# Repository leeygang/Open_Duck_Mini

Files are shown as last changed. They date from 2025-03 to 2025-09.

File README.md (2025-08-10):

# Open Duck Mini v2

<table>
  <tr>
    <td> </td>
    <td> </td>
    <td> </td>
   </tr> 
</table>

We are making a miniature version of the BDX Droid by Disney. It is about 42 centimeters tall with its legs extended.
The full BOM cost should be under $400 !

This repo is kind of a hub where we centralize all resources related to this project. This is a working repo, so there are a lot of undocumented scripts :) We'll try to clean things up at some point.

# State of sim2real

https://github.com/user-attachments/assets/58721d0f-2f95-4088-8900-a5d02f41bba7

https://github.com/user-attachments/assets/4129974a-9d97-4651-9474-c078043bb182

https://github.com/user-attachments/assets/a0afcd38-15d8-40c6-8171-a619107406b8

# Updates

> Update 02/04/2024: You can try two policies we trained : [this one](BEST_WALK_ONNX.onnx) and [this one](BEST_WALK_ONNX_2.onnx)
> Run with the following arguments :
> python v2_rl_walk_mujoco.py --onnx_model_path ~/BEST_WALK_ONNX_2.onnx

> Update 15/03/2025: join our discord server to get help or show us your duck :) https://discord.gg/UtJZsgfQGe

> Update 07/02/2025: Big progress on sim2real, see videos above :)

> Update 24/02/2025: Working hard on sim2real ! 

> Update 07/02/2025 : We are writing documentation on the go, but the design and BOM should not change drastically. Still missing the "expression" features, but they can be added after building the robot!

> Update 22/01/2025 : The mechanical design is pretty much finalized (fixing some mistakes here and there). The current version does not include all the "expression" features we want to include in the final robot (LEDs for the eyes, a camera, a speaker and a microphone). We are now working on making it walk with reinforcement learning !

# Community 

duck_collage

Join our discord community ! https://discord.gg/UtJZsgfQGe

# CAD

https://cad.onshape.com/documents/64074dfcfa379b37d8a47762/w/3650ab4221e215a4f65eb7fe/e/0505c262d882183a25049d05

See [this document](docs/prepare_robot.md) for getting from a onshape design to a simulated robot in MuJoCo (Warning, outdated. Has not been updated in a while)

# RL stuff

We are switching to Mujoco Playground, see this [repo](https://github.com/apirrone/Open_Duck_Playground)

https://github.com/user-attachments/assets/037a1790-7ac1-4140-b154-2c901d20d5f5

## Reference motion generation for imitation learning 

https://github.com/user-attachments/assets/4cb52e17-99a5-47a8-b841-4141596b7afb

See [this repo](https://github.com/apirrone/Open_Duck_reference_motion_generator)

## Actuator identification 

We used Rhoban's [BAM](https://github.com/Rhoban/bam)

# BOM

https://docs.google.com/spreadsheets/d/1gq4iWWHEJVgAA_eemkTEsshXqrYlFxXAPwO515KpCJc/edit?usp=sharing

Chinese: https://zihao-ai.feishu.cn/wiki/AfAtw69vRigXaRk5UkbcrAiLnJw?from=from_copylink

# Build Guide

Chinese: https://zihao-ai.feishu.cn/wiki/space/7488517034406625281

## Print Guide

See [print_guide](docs/print_guide.md).

## Assembly Guide

See [assembly guide (incomplete)](docs/assembly_guide.md).

# Embedded runtime

This repo contains the code to run the policies on the onboard computer (Raspberry pi zero 2w) https://github.com/apirrone/Open_Duck_Mini_Runtime

# Training your own policies

If you want to train your own policies, and contribute to making the ducks walk nicely, see [this document](docs/sim2real.md)

> Thanks a lot to HuggingFace and Pollen Robotics for sponsoring this project !

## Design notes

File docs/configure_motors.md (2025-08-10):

# Configure the motors

> This sould be done independently on each motor *before* builiding the duck.
>
> During the process, the motor will move to its zero position. You can then install the horn while trying to align it the best you can like in the photo below. (Don't worry if it's not perfect, we will compensate for that later)

Capture d’écran du 2025-04-25 09-55-34

Clone and install (`pip install -e .`) the runtime repo on the `v2` branch : `https://github.com/apirrone/Open_Duck_Mini_Runtime`

You can either install it on your own computer or on the raspberry pi for the configuration, as you want. You'll just want a way to power the servos, for example, the battery pack.

Then for each motor, run the following command : 

```bash
python configure_motor.py --id <id>
```

The motors ids are : 

```python
{
    "left_hip_yaw": 20,
    "left_hip_roll": 21,
    "left_hip_pitch": 22,
    "left_knee": 23,
    "left_ankle": 24,
    "neck_pitch": 30,
    "head_pitch": 31,
    "head_yaw": 32,
    "head_roll": 33,
    "right_hip_yaw": 10,
    "right_hip_roll": 11,
    "right_hip_pitch": 12,
    "right_knee": 13,
    "right_ankle": 14,
}
```

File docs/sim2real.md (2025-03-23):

> Not finalized yet

# Training policies that transfer to the real robot (sim2real)

We want to train policies that transfer well to the real robot. This is the sim2real problem. It's a hard problem, especially for us since we are using cheap servomotors that are hard to model and not overly powerful. 

Below, I'll roughly explain the steps we went through to get there, but you won't have to do everything again yourself since we provide the results of each process.

## Make an accurate model of the robot (URDF/MJCF)

### Robot structure

In the [Onhape document](https://cad.onshape.com/documents/64074dfcfa379b37d8a47762/w/3650ab4221e215a4f65eb7fe/e/0505c262d882183a25049d05), we specify the material of each part. But to be more accurate, because we print with infill we override the mass of the parts with the (pretty accurate) estimation of the slicer. 

We use [onshape-to-robot](https://github.com/Rhoban/onshape-to-robot) to export URDF/MJCF descriptions. For MJX, we have to make a lightweight model, see our [config.json](https://github.com/apirrone/Open_Duck_Playground/blob/main/playground/open_duck_mini_v2/xmls/config.json). 

This gives us a MJCF (Mujoco format) [description of the robot](https://github.com/apirrone/Open_Duck_Playground/blob/main/playground/open_duck_mini_v2/xmls/open_duck_mini_v2.xml) which describes the masses and moments of inertia of the full robot. 

### Motors

Another very important part of having an accurate model is modeling the motors's behavior. We use [BAM](https://github.com/Rhoban/bam/) for that. You don't have to go through the identification process yourself, we provide the results [here](https://github.com/Rhoban/bam/tree/main/params/feetech_sts3215_7_4V)

It's critical that the simulator simulates the motors accurately, because we will train a policy (a neural network) to output motor positions based on sensory inputs (motors positions/speeds, imu and feet sensors). If the motors behave differently in the simulation than in the real world, the policy won't work, or at worst, produce chaotic movements.

`BAM` allows us to export the main identified parameters to mujoco units (using `bam.to_mujoco`). These values are the ones we set in out mjcf model for the actuators and joints properties. 

- damping
- kp
- frictionloss
- armature
- forcerange

## Training policies 

We use our own [mujoco playground](https://github.com/google-deepmind/mujoco_playground) based framework, [Open Duck Playground](https://github.com/apirrone/Open_Duck_Playground)

In the [joystick](https://github.com/apirrone/Open_Duck_Playground/blob/main/playground/open_duck_mini_v2/joystick.py) env, you can try to enable/disable different rewards, write your own, play with the weights, noise, randomization etc. 

We obtained good results by implementing the imitation reward described by Disney in their [BDX paper](https://github.com/apirrone/Open_Duck_Playground/blob/main/playground/open_duck_mini_v2/joystick.py). 

To use this reward, we need reference motion. We made [this repo](https://github.com/apirrone/Open_Duck_reference_motion_generator) to generate such motion using a parametric walk engine. Following the instructions there, you can generate a `polynomial_coefficients.pkl` file which contains the reference motions. There is already such a file in the playground repo under the `data/` directory. 

Once your policy is trained, you can try to run it on the real robot using [this script](https://github.com/apirrone/Open_Duck_Mini_Runtime/blob/v2/scripts/v2_rl_walk_mujoco.py) in the runtime repo. Make sure you completed all the steps in the [checklist](https://github.com/apirrone/Open_Duck_Mini_Runtime/blob/v2/checklist.md) before running this.

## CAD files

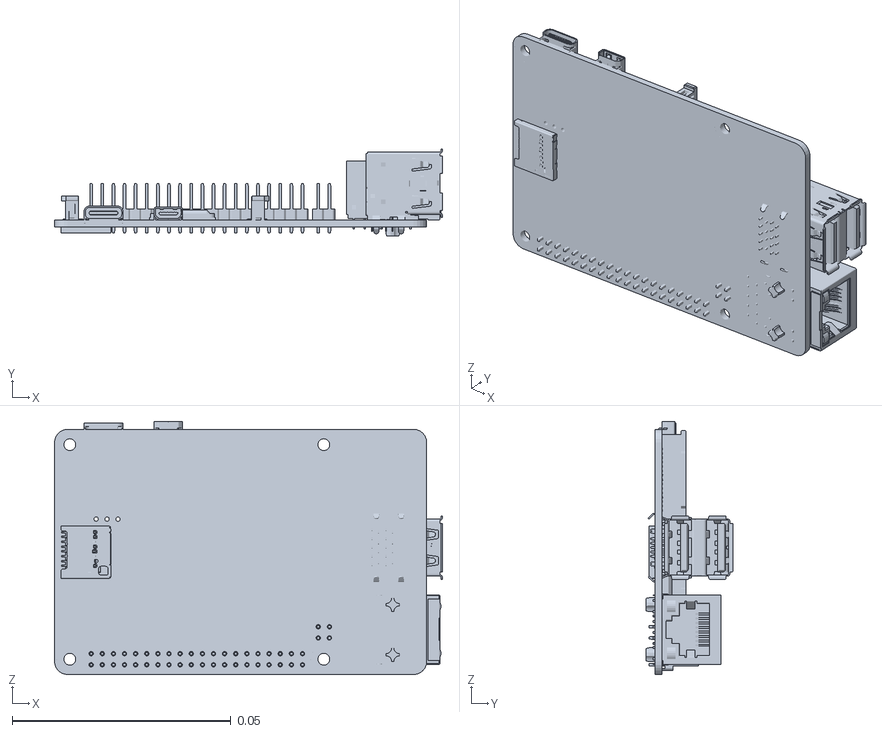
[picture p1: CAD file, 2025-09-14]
wild/assets/rp_assemble.stl
0.0886 x 0.0199 x 0.0578

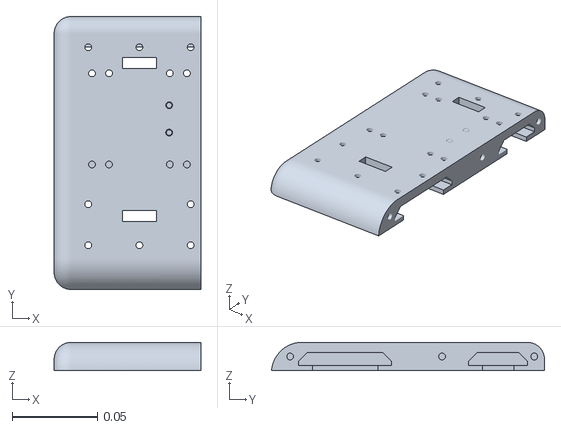
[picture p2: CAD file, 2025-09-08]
wild/assets/foot_main.stl
0.086 x 0.16 x 0.0166

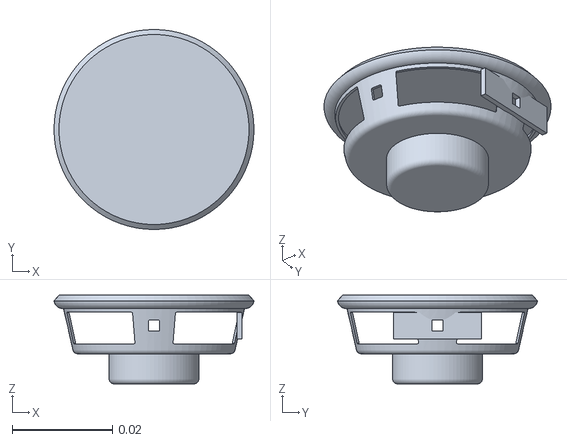
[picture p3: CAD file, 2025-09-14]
robotb/assets/full_speaker.stl
0.0399 x 0.0399 x 0.0177

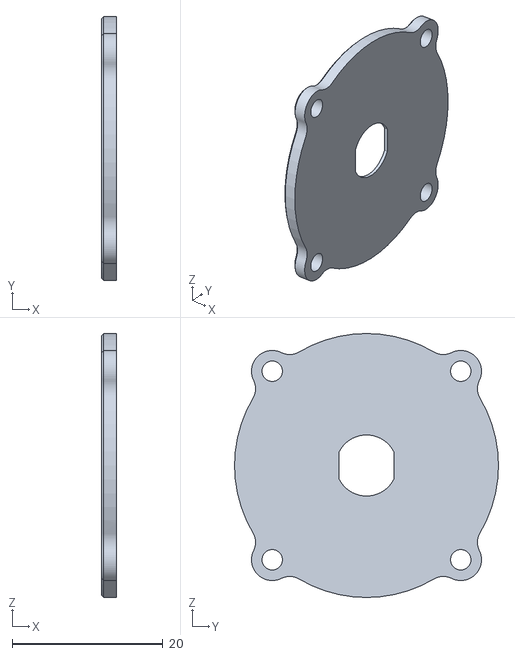
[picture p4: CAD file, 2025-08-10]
print/bulb.stl
2.00 x 35.0 x 35.0

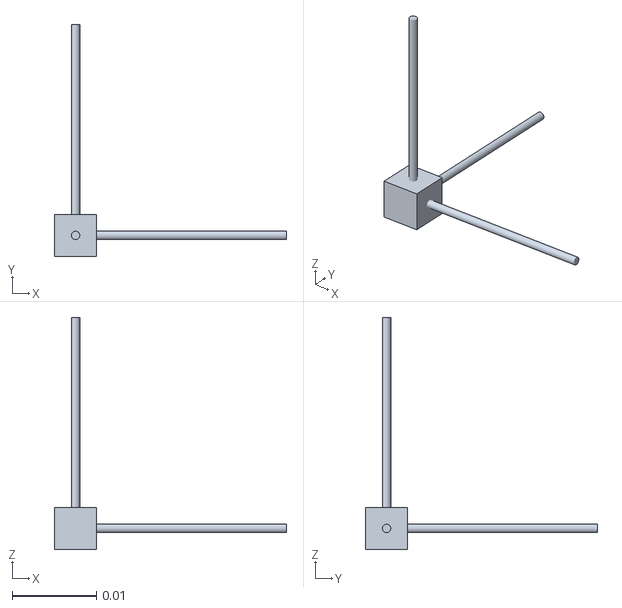
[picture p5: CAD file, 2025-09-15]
robotb/assets/frame.stl
0.0275 x 0.0275 x 0.0275

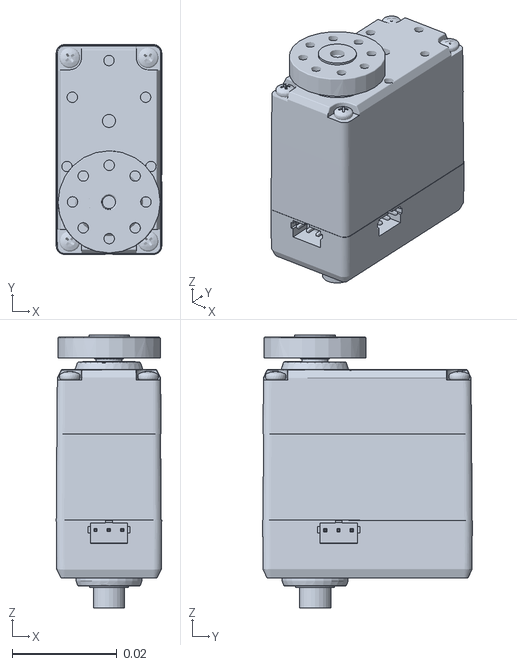
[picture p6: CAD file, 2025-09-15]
wild/assets/htd_45h_1circle.stl
0.0201 x 0.04 x 0.0521

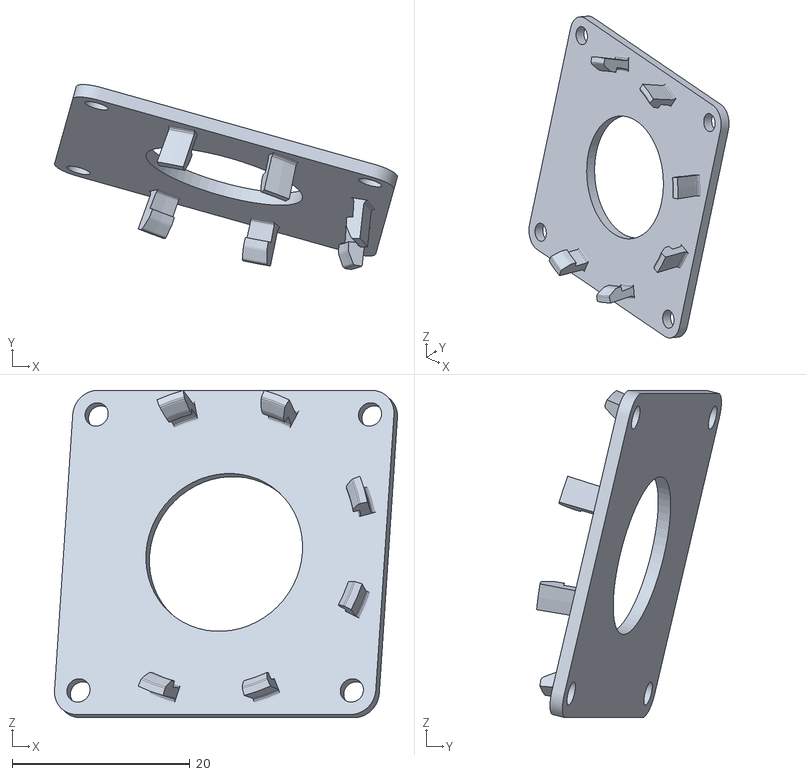
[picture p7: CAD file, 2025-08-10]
print/speaker_interface.stl
38.6 x 20.8 x 36.9

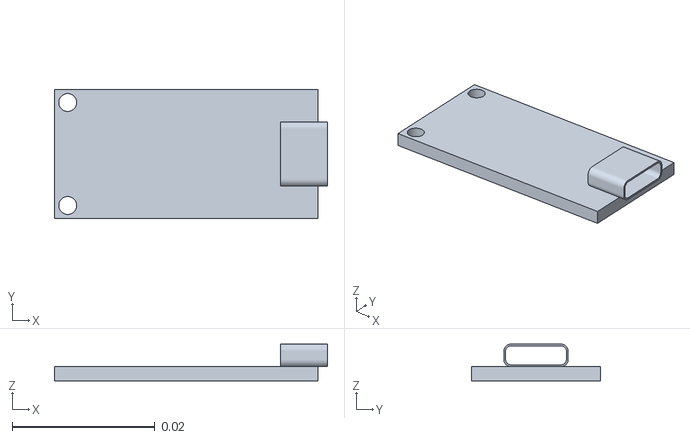
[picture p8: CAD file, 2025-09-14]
robotb/assets/usb_c_charger.stl
0.0382 x 0.0181 x 0.00515

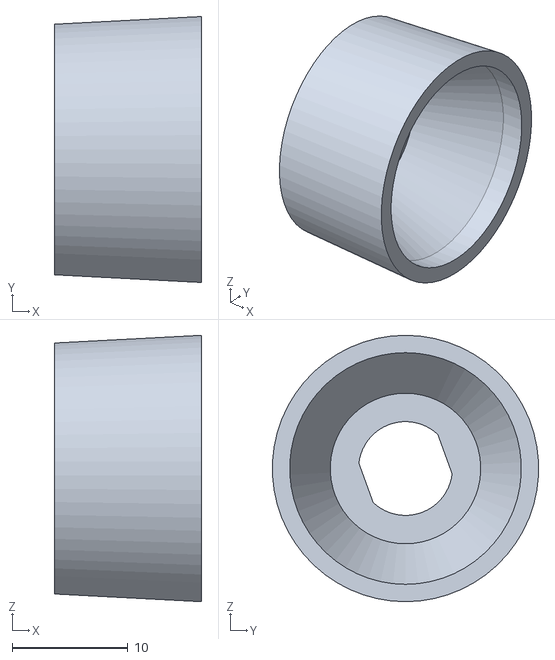
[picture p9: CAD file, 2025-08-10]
print/flash_reflector_interface.stl
12.7 x 23.0 x 23.0

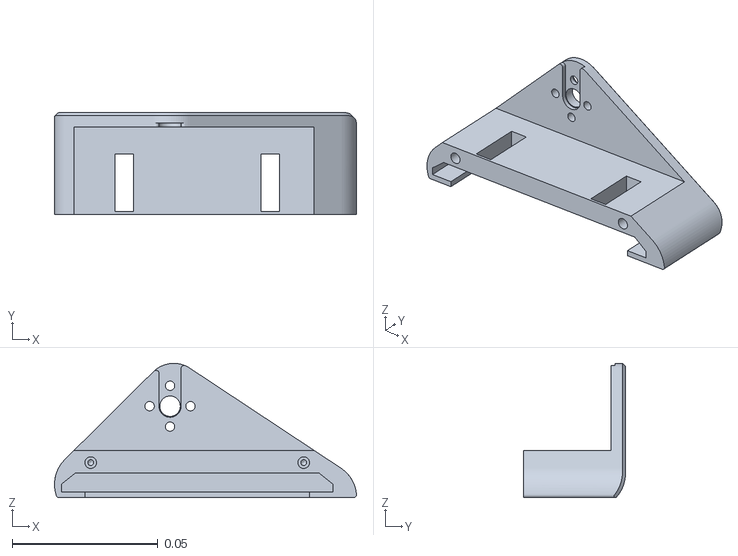
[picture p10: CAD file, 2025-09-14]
robotb/assets/foot_top.stl
0.103 x 0.0349 x 0.046

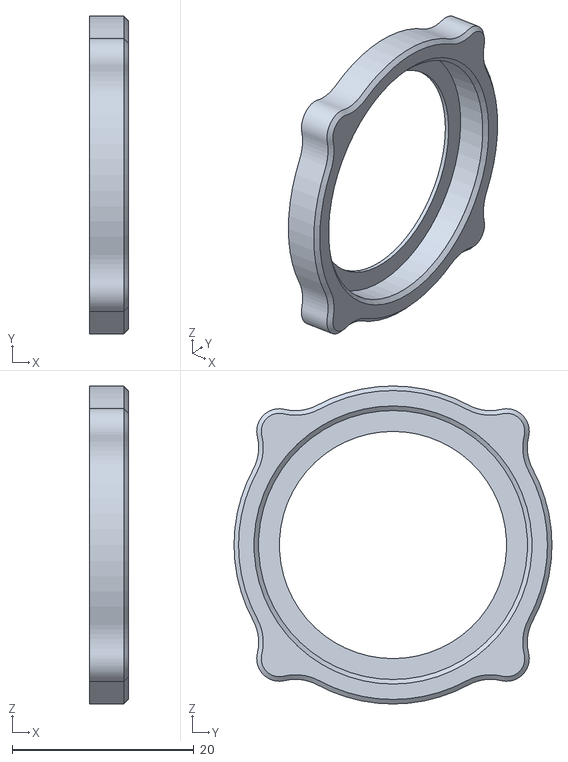
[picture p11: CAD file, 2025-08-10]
print/left_eye.stl
4.30 x 35.0 x 35.0

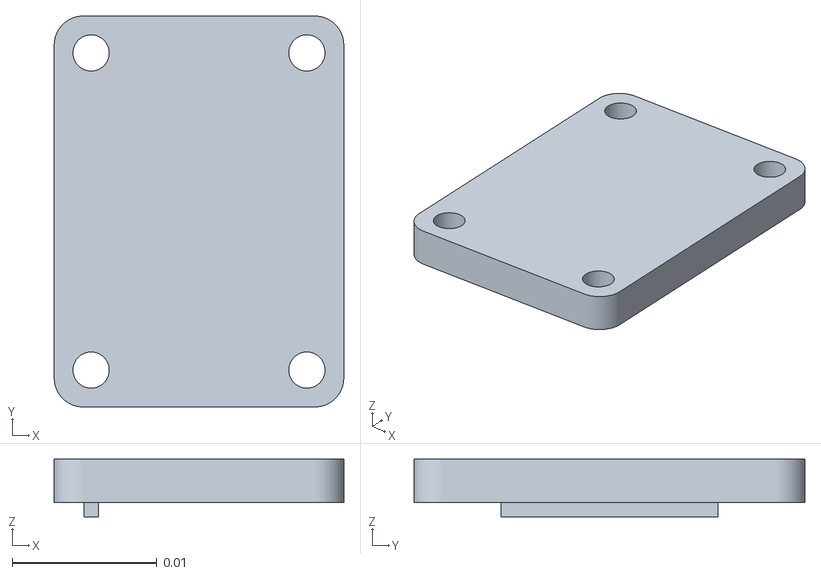
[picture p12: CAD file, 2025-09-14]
robotb/assets/bno055.stl
0.02 x 0.027 x 0.004

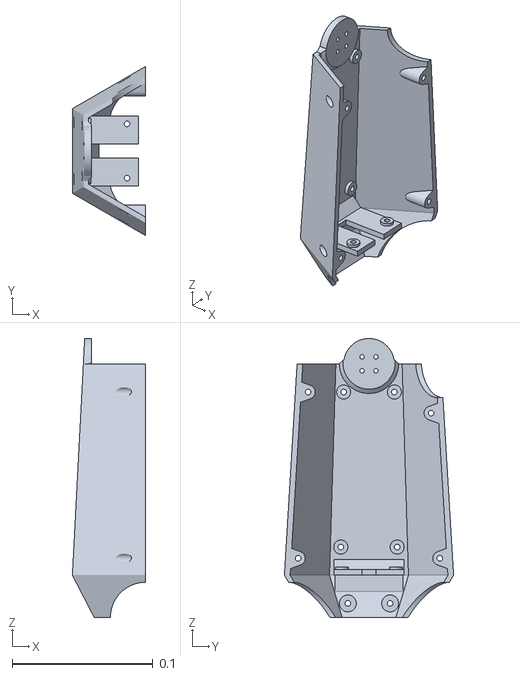
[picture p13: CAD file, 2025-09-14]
wild/assets/low_leg_left.stl
0.052 x 0.12 x 0.198

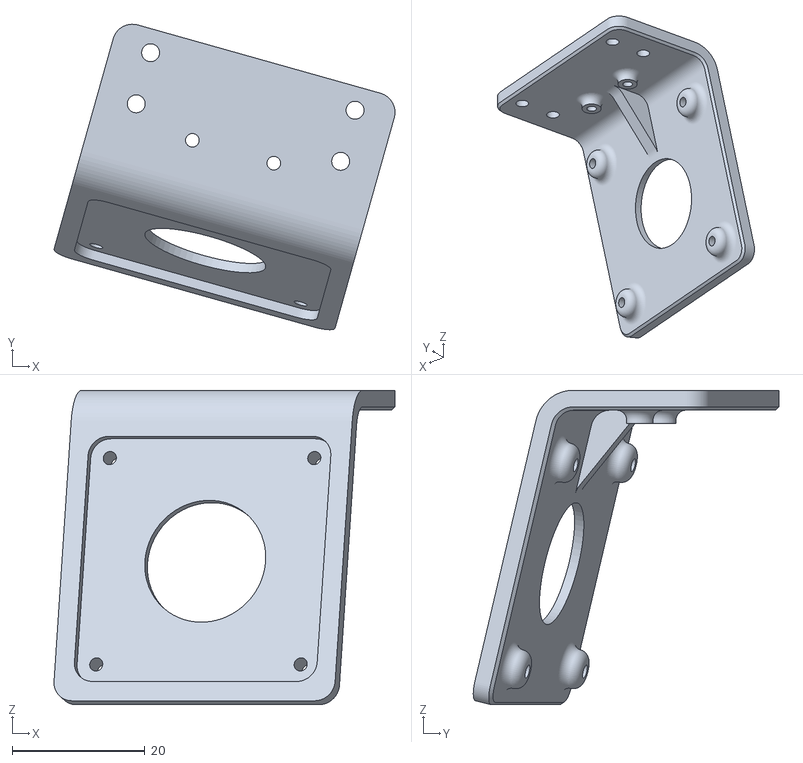
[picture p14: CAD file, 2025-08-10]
print/speaker_stand.stl
51.4 x 46.0 x 47.4

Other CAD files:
wild/assets/foot_main_right.stl
robotb/assets/roll_motor_top.stl
wild/assets/low_leg_right.stl
print/flash_light_module.stl
print/right_eye.stl
robotb/assets/antenna.stl
robotb/assets/battery_pack_lid.stl
robotb/assets/bms.stl
robotb/assets/board.stl
robotb/assets/body_back.stl
robotb/assets/body_front.stl
robotb/assets/body_middle_bottom.stl
robotb/assets/body_middle_top.stl
robotb/assets/bulb.stl
robotb/assets/cam.stl
robotb/assets/cell.stl
robotb/assets/drive_palonier.stl
robotb/assets/flash_light_module.stl
robotb/assets/flash_reflector_interface.stl
robotb/assets/foot_bottom_pla.stl
robotb/assets/foot_bottom_tpu.stl
robotb/assets/foot_side.stl
robotb/assets/glass.stl
robotb/assets/head.stl
robotb/assets/head_bot_sheet.stl
robotb/assets/head_pitch_to_yaw.stl
robotb/assets/head_roll_mount.stl
robotb/assets/head_yaw_to_roll.stl
robotb/assets/holder.stl
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

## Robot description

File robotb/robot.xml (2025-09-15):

<?xml version="1.0" ?>
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
<mujoco model="robotb">
  <compiler angle="radian" meshdir="assets" autolimits="true"/>
  <default>
    <default class="robotb">
      <joint frictionloss="0.1" armature="0.005"/>
      <position kp="50" dampratio="1"/>
      <default class="visual">
        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
      </default>
      <default class="collision">
        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
      </default>
    </default>
  </default>
  <worldbody>
    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
    <body name="trunk_assembly" pos="0 0 0" quat="1 0 0 0" childclass="robotb">
      <freejoint name="trunk_assembly_freejoint"/>
      <inertial pos="-0.0483271 -9.97796e-05 0.0384971" mass="0.698545" fullinertia="0.00167701 0.00344483 0.00292639 -1.31661e-05 -3.24929e-05 -2.15582e-06"/>
      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
      <body name="hip_roll_assembly" pos="-0.019 0.035 0.0459409" quat="0.965926 -2.75967e-15 -1.08802e-14 0.258819">
        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
        <joint axis="0 0 1" name="left_hip_yaw" type="hinge" range="-1.0471975511965963 1.3322676295501878e-15"/>
        <inertial pos="0.000795081 -5.46541e-06 -0.03306" mass="0.06648" fullinertia="2.44411e-05 2.81818e-05 1.42687e-05 2.35658e-09 -3.81059e-07 -7.50036e-09"/>
        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
        <body name="left_roll_to_pitch_assembly" pos="0.01905 7.14619e-15 -0.046015" quat="0.401729 -0.581905 -0.401729 0.581905">
          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
          <joint axis="0 0 1" name="left_hip_roll" type="hinge" range="-0.7986645746476461 0.0740000513495187"/>
          <inertial pos="0.0507497 -0.000407512 0.0204377" mass="0.07516" fullinertia="2.52682e-05 4.15738e-05 2.82869e-05 1.22744e-07 -7.32857e-07 -1.05692e-07"/>
          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
          <body name="knee_and_ankle_assembly" pos="0.07415 -3.52149e-16 0.03511" quat="0.0540509 -0.705038 -0.0540509 0.705038">
            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
            <joint axis="0 0 1" name="left_hip_pitch" type="hinge" range="-1.068702275442209 0.6766269765521203"/>
            <inertial pos="0.00253369 -0.0390636 0.0102776" mass="0.12407" fullinertia="0.000211406 7.83759e-05 0.000225619 -2.68706e-05 3.81906e-06 2.08009e-05"/>
            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
            <body name="knee_and_ankle_assembly_2" pos="9.02056e-17 -0.07865 0.0001" quat="0.907953 -7.9042e-16 -2.02408e-15 0.419073">
              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
              <joint axis="0 0 1" name="left_knee" type="hinge" range="-2.435644371861684 0.705948281728109"/>
              <inertial pos="5.01859e-06 -0.0577465 0.0181136" mass="0.07259" fullinertia="4.99575e-05 1.87273e-05 4.23932e-05 1.03817e-08 2.25175e-09 8.81049e-08"/>
              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
              <body name="foot_assembly" pos="1.38778e-17 -0.07865 0.0001" quat="0.937075 -1.05057e-16 -2.02087e-16 -0.349129">
                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
                <joint axis="0 0 1" name="left_ankle" type="hinge" range="-0.8575140382901978 2.2840786152995953"/>
                <inertial pos="0.0110718 -0.0246608 0.0190626" mass="0.07524" fullinertia="1.87482e-05 6.74427e-05 6.061e-05 1.58839e-06 -6.52354e-09 5.67391e-08"/>
                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
              </body>
            </body>
          </body>
        </body>
      </body>
      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
      <body name="neck_pitch_assembly" pos="0.001 0.01915 0.0900009" quat="0.707107 0.707107 -7.85046e-15 7.82373e-15">
        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
        <joint axis="0 0 1" name="neck_pitch" type="hinge" range="-0.3490658503988437 1.1344640137963364"/>
        <inertial pos="-5.63137e-06 0.0492968 0.0181786" mass="0.06618" fullinertia="3.49456e-05 1.70231e-05 2.80043e-05 8.75633e-09 -2.15592e-09 -1.85188e-08"/>
        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
        <body name="head_pitch_to_yaw" pos="-5.44269e-17 0.066 -5.36443e-18" quat="1 -5.59807e-17 -1.11022e-16 2.77556e-17">
          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
          <joint axis="0 0 1" name="head_pitch" type="hinge" range="-0.7853981633974483 0.7853981633974483"/>
          <inertial pos="-0.00766247 0.026015 0.0186681" mass="0.0169378" fullinertia="9.43036e-06 4.64763e-06 8.02915e-06 1.35195e-06 3.05899e-08 -8.42802e-08"/>
          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
          <body name="neck_yaw_assembly" pos="-1.43115e-17 0.057 0.01905" quat="0.707107 -0.707107 -6.28037e-16 5.00467e-16">
            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
            <joint axis="0 0 1" name="head_yaw" type="hinge" range="-2.7925268031909254 2.792526803190929"/>
            <inertial pos="0.00412907 3.95745e-06 -0.0222828" mass="0.0918099" fullinertia="3.11706e-05 6.94935e-05 7.04025e-05 4.29429e-09 -4.41251e-06 -3.82028e-09"/>
            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
            <body name="head_assembly" pos="0.04095 -1.78376e-16 -0.01915" quat="0.707107 -2.89486e-16 -0.707107 -2.75741e-16">
              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
              <joint axis="0 0 1" name="head_roll" type="hinge" range="-0.523598775598297 0.5235987755983006"/>
              <inertial pos="0.00815617 -0.0039342 0.0227894" mass="0.406607" fullinertia="0.00244582 0.00168662 0.00107943 -2.00028e-06 9.23825e-05 -1.90734e-05"/>
              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
            </body>
          </body>
        </body>
      </body>
      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
      <body name="hip_roll_assembly_2" pos="-0.019 -0.035 0.0459409" quat="1 -1.11022e-16 -1.12133e-14 -6.45919e-15">
        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
        <joint axis="0 0 1" name="right_hip_yaw" type="hinge" range="-0.5235987755982855 0.5235987755983121"/>
        <inertial pos="0.000795081 -5.46541e-06 -0.03306" mass="0.06648" fullinertia="2.44411e-05 2.81818e-05 1.42687e-05 2.35658e-09 -3.81059e-07 -7.50036e-09"/>
        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
        <body name="right_roll_to_pitch_assembly" pos="0.01905 4.63733e-14 -0.046015" quat="0.5 -0.5 -0.5 0.5">
          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
          <joint axis="0 0 1" name="right_hip_roll" type="hinge" range="-0.43633231299856995 0.4363323129985948"/>
          <inertial pos="-0.0507497 -0.000417205 0.0204377" mass="0.07516" fullinertia="2.52676e-05 4.15738e-05 2.82863e-05 -1.31172e-07 7.32857e-07 -8.94684e-08"/>
          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
          <body name="knee_and_ankle_assembly_3" pos="-0.07415 -1.58565e-18 0.03511" quat="0.707107 -2.34656e-14 0.707107 -2.34848e-14">
            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
            <joint axis="0 0 1" name="right_hip_pitch" type="hinge" range="-0.5235987755982322 1.2217304763960972"/>
            <inertial pos="0.00253369 0.0390636 0.010809" mass="0.12407" fullinertia="0.000212363 7.93324e-05 0.000225619 2.68706e-05 3.9656e-06 -2.17407e-05"/>
            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
            <body name="knee_and_ankle_assembly_4" pos="-3.46945e-17 0.07865 0.037" quat="3.2942e-17 0.997412 0.0718931 -2.9738e-17">
              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
              <joint axis="0 0 1" name="right_knee" type="hinge" range="-1.4268860704567814 1.7147065831330117"/>
              <inertial pos="5.01859e-06 -0.0577465 0.0181136" mass="0.07259" fullinertia="4.99575e-05 1.87273e-05 4.23932e-05 1.03817e-08 2.25175e-09 8.81049e-08"/>
              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
              <body name="foot_assembly_2" pos="-2.08167e-17 -0.07865 0.0001" quat="0.999847 -0 4.22926e-18 0.0175054">
                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
                <joint axis="0 0 1" name="right_ankle" type="hinge" range="-1.6058088572068765 1.5357837963829166"/>
                <inertial pos="0.0110718 -0.0246608 0.0190626" mass="0.07524" fullinertia="1.87482e-05 6.74427e-05 6.061e-05 1.58839e-06 -6.52354e-09 5.67391e-08"/>
                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
              </body>
            </body>
          </body>
        </body>
      </body>
    </body>
  </worldbody>
  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
  <actuator>
    <position class="robotb" name="left_hip_yaw" joint="left_hip_yaw" inheritrange="1"/>
    <position class="robotb" name="left_hip_roll" joint="left_hip_roll" inheritrange="1"/>
    <position class="robotb" name="left_hip_pitch" joint="left_hip_pitch" inheritrange="1"/>
    <position class="robotb" name="left_knee" joint="left_knee" inheritrange="1"/>
    <position class="robotb" name="left_ankle" joint="left_ankle" inheritrange="1"/>
    <position class="robotb" name="neck_pitch" joint="neck_pitch" inheritrange="1"/>
    <position class="robotb" name="head_pitch" joint="head_pitch" inheritrange="1"/>
    <position class="robotb" name="head_yaw" joint="head_yaw" inheritrange="1"/>
    <position class="robotb" name="head_roll" joint="head_roll" inheritrange="1"/>
    <position class="robotb" name="right_hip_yaw" joint="right_hip_yaw" inheritrange="1"/>
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

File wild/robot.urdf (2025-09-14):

<?xml version="1.0" ?>
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
<robot name="wild">
  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
  <link name="waist">
    <inertial>
      <origin xyz="-4.83602e-05 0.00168668 -0.0137073" rpy="0 0 0"/>
      <mass value="0.438621"/>
      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
    </inertial>
    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
  </link>
  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
  <link name="chassis">
    <inertial>
      <origin xyz="0.00235226 0.00416672 -0.0682563" rpy="0 0 0"/>
      <mass value="0.841214"/>
      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
    </inertial>
    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
  </link>
  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
  <joint name="waist" type="revolute">
    <origin xyz="2.43399e-05 -0.000217894 0.0284972" rpy="3.14043 0.000826419 -9.6369e-07"/>
    <parent link="waist"/>
    <child link="chassis"/>
    <axis xyz="0 0 1"/>
    <limit effort="10" velocity="10" lower="-1.5708" upper="1.5708"/>
  </joint>
  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
  <link name="left_hip">
    <inertial>
      <origin xyz="-0.00246743 -0.00911137 -0.0331054" rpy="0 0 0"/>
      <mass value="0.0849728"/>
      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
    </inertial>
    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
  </link>
  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
  <link name="upper_leg">
    <inertial>
      <origin xyz="0.0239606 0.15748 0.0267038" rpy="0 0 0"/>
      <mass value="0.236189"/>
      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
    </inertial>
    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
  </link>
  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
  <link name="lower_leg">
    <inertial>
      <origin xyz="-0.000521353 -0.101401 0.0270619" rpy="0 0 0"/>
      <mass value="0.380663"/>
      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
    </inertial>
    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
  </link>
  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
  <link name="ankle">
    <inertial>
      <origin xyz="-0.000778386 -0.0291765 0.0259275" rpy="0 0 0"/>
      <mass value="0.0230191"/>
      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
    </inertial>
    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
  </link>
  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
  <link name="left_foot">
    <inertial>
      <origin xyz="-0.0183724 -0.00183888 0.00908589" rpy="0 0 0"/>
      <mass value="0.413618"/>
      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
    </inertial>
    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
  </link>
  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
  <joint name="left_foot" type="revolute">
    <origin xyz="-0.0268 -0.0594 0.0268" rpy="1.5708 -0.349066 1.5708"/>
    <parent link="ankle"/>
    <child link="left_foot"/>
    <axis xyz="0 0 1"/>
    <limit effort="10" velocity="10" lower="0" upper="0"/>
  </joint>
  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
  <joint name="left_ankle" type="revolute">
    <origin xyz="-4.74705e-05 -0.179984 0.000442075" rpy="0.00142308 0.000132648 0.523599"/>
    <parent link="lower_leg"/>
    <child link="ankle"/>
    <axis xyz="0 0 1"/>
    <limit effort="10" velocity="10" lower="0" upper="0"/>
  </joint>
  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
  <joint name="left_knee" type="revolute">
    <origin xyz="0.00366073 0.194183 0.0267" rpy="-0.573319 -1.57079 -2.72581"/>
    <parent link="upper_leg"/>
    <child link="lower_leg"/>
    <axis xyz="0 0 1"/>
    <limit effort="10" velocity="10" lower="-2.92267e-10" upper="1.5708"/>
  </joint>
  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
  <joint name="left_hip" type="revolute">
    <origin xyz="-0.0268591 -0.00149279 -0.0365475" rpy="8.076e-13 1.56997 0.0505006"/>
    <parent link="left_hip"/>
    <child link="upper_leg"/>
    <axis xyz="0 0 1"/>
    <limit effort="10" velocity="10" lower="-0.889656" upper="0.506607"/>
  </joint>
  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
  <joint name="left_waist_hip" type="revolute">
    <origin xyz="0.0535826 -0.000150648 -0.0532864" rpy="-1.57196 9.6369e-07 1.57162"/>
    <parent link="waist"/>
    <child link="left_hip"/>
    <axis xyz="0 0 1"/>
    <limit effort="10" velocity="10" lower="-0.572933" upper="1.52146"/>
  </joint>
  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
  <link name="right_hip">
    <inertial>
      <origin xyz="0.00208458 -0.00914794 -0.0331404" rpy="0 0 0"/>
      <mass value="0.0849728"/>
      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
    </inertial>
    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
  </link>
  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
  <link name="upper_leg_2">
    <inertial>
      <origin xyz="-0.000145579 0.159292 0.0267038" rpy="0 0 0"/>
      <mass value="0.236189"/>
      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
    </inertial>
    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
  </link>
  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
  <link name="lower_leg_2">
    <inertial>
      <origin xyz="-0.000521353 0.101401 0.0223802" rpy="0 0 0"/>
      <mass value="0.380663"/>
      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
    </inertial>
    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
  </link>
  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
  <link name="ankle_2">
    <inertial>
      <origin xyz="-0.000778386 -0.0291765 0.0259275" rpy="0 0 0"/>
      <mass value="0.0230191"/>
      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
    </inertial>
    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
  </link>
  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
  <link name="right_foot">
    <inertial>
      <origin xyz="0.0182015 0.00183892 -0.0102852" rpy="0 0 0"/>
      <mass value="0.413618"/>
      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
    </inertial>
    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
  </link>
  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
  <joint name="right_foot" type="revolute">
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

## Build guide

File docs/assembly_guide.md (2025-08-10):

# Assembly guide

> Before assembling the duck, you should first [configure your motors](./configure_motors.md)

## Requirements : 

You will need : 
- A soldering iron, and basic electronics tools and skills
- X m3 screws (TODO : add the exact number)
- Some wire
- Loctite Threadlocker blue 243

> General note : Everytime you screw something in the motors metal against metal, you want to use a little loctite threadlocker. This will prevent the screws from coming loose due to the vibrations during the operation of the robot. It adds a little time to to the build, but you'll be glad you took the time ;)
>
> Don't use loctite with the plastic screws

> At any time, you can refer to the CAD here : https://cad.onshape.com/documents/64074dfcfa379b37d8a47762/w/3650ab4221e215a4f65eb7fe/e/0505c262d882183a25049d05

## Steps :

### Assemble the trunk

Place the bearings in `trunk_bottom` like so, and insert M3 inserts in these holes. It's also a good time to insert the 4 M3 inserts in the bottom of this part to mount body parts later on.



Then assamble `trunk_bottom` and `trunk_top`, and screw them together with 2 `M3x10` screws through these holes



Mount the middle motor like so and screw it with the plastic screws that came with the motors : 



Insert `roll_motor_bottom` like this 



### Assemble the feet

Both feet are the same. 

First, assemble `foot_bottom_tpu` with `foot_bottom_pla`. Insert M3 inserts in these holes :



And screw the two parts together with two `M3x6` screws.

Then, insert M3 inserts in these holes in `foot_top` here : 



And assemble everything like so. Make sure the driver side of the motor is on the `foot_top` part side : 

<table>
  <tr>
    <td>  </td>
    <td>  </td>
   </tr> 
</table>

You can add the foot switches like this too :

> You press fit them so that the switch is activated when the foot touches the ground

<table>
  <tr>
    <td>  </td>
    <td>  </td>
   </tr> 
</table>

### Assemble the shins

Insert M3 Inserts in these holes of `leg_spacer` (on both sides. Insert 4 M3 inserts in total) :



Then, first plug the motor cable in the foot's motor, and make it go through the `right_sheet` like so 



Then assemble like below:



### Assemble the thighs 

The thigh is pretty much the same thing, except the `hip_pitch` motor is mounted this way (important for the zero position)



### Assemble the hips

Mount `left_roll_to_pitch` or `right_roll_to_pitch`, here the parts are symmetrical so you have to use the right one.



Mount `roll_motor_top` to the `hip_yaw` servo (screw from the bottom). Don't mount the servo to the trunk yet.



Then mount `hip_roll` like this 



And insert the sub assembly like this 



Screw everything you can (with the plastic screws provided with the servos)

You can now mount the leg like this :



And do the same for the other leg :)

Your duck should now look like this 



### Assemble the neck

You know the drill



### Assemble the head mechanism

First, mount `head_pitch_to_yaw` like this 



Then, independently mount `head_yaw_to_roll` and `head_roll_mount` to `head_roll dof`



(You can insert `head_bot_plate` and `body_middle_top` now too to avoid having to disassamble the head later)

Then 



Then 



Your duck should now look like this 



### Mount the servo driver board

TODO take a photo

### Mount the IMU

Like this 

> It's actually better to mount the IMU with the correct natural orientation, which would be flipped along the X axis compared to the pictures below
> In the picture below, the IMU is mounted upside down.
> It probably doesn't really matter a lot if you mount it upside down or not. You can configure how you mounted it later

<table>
  <tr>
    <td> </td>
    <td> </td>
   </tr> 
</table>

## Electronics

Here is the global electonics schematic for reference 

<table>
  <tr>
    <td> </td>
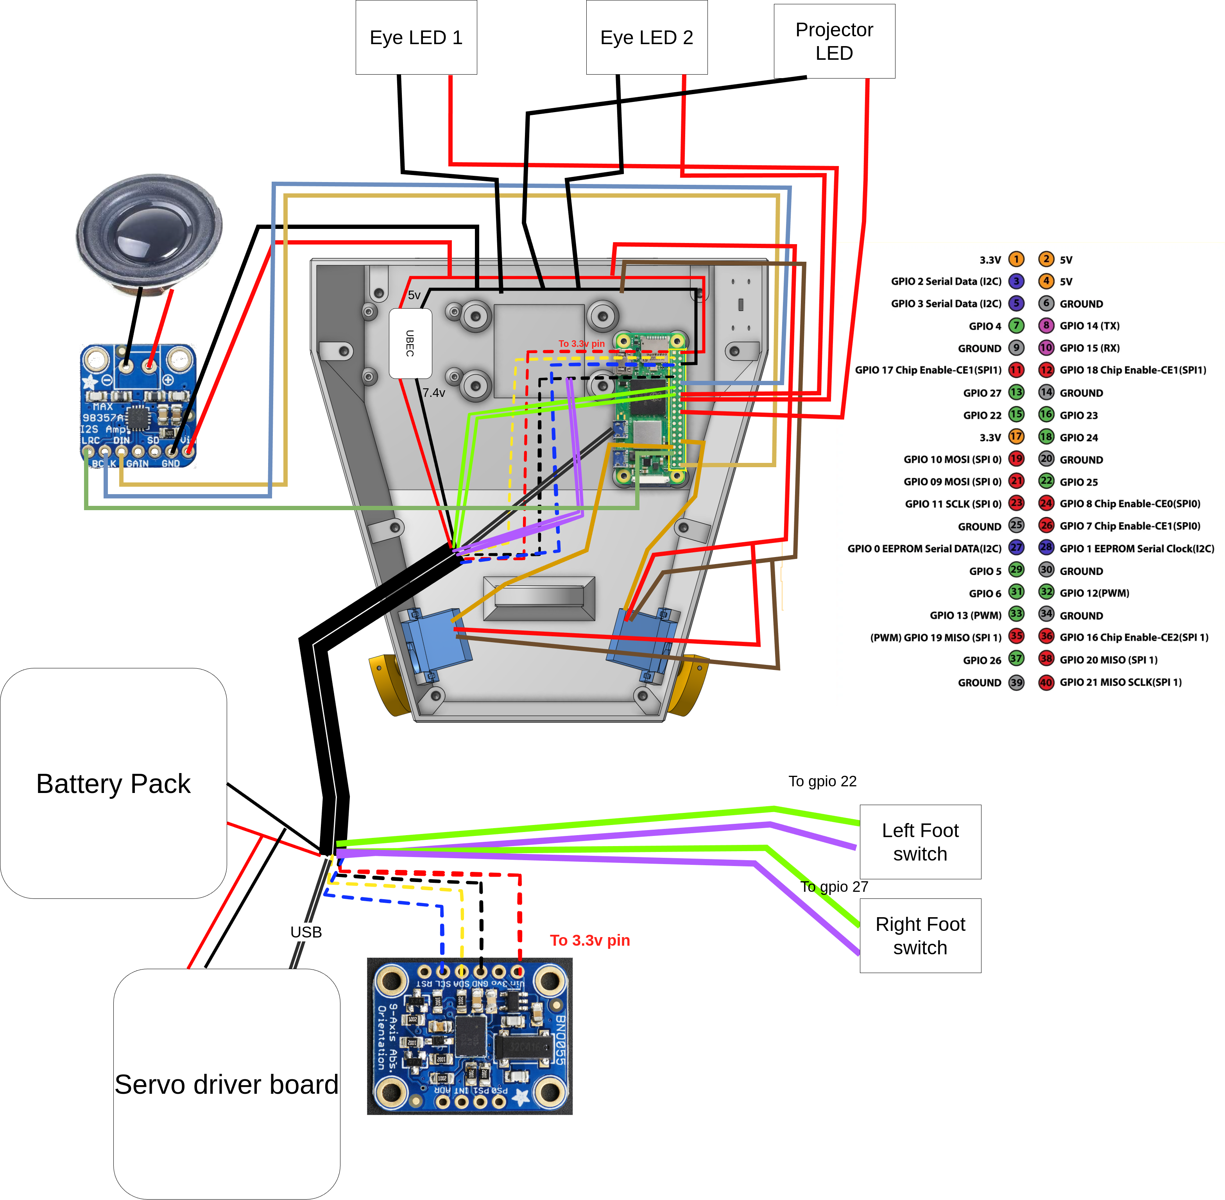
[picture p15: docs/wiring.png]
    <td> </td>
   </tr> 
</table>

Here is how to wire the feet 

feet

### Battery pack

> To be safe, make sure your cells are charged to the same voltage before placing them in the holder.

<table>
  <tr>
    <td> </td>
    <td> </td>
   </tr> 
</table>

### Head

First, insert the M3 inserts in all these holes 



> TODO add instructions for expression features (camera, antennas, eye leds, projector and speaker)

Then insert the bearing, mount the ear motors and the raspberry pi zero 2w.

For reference, the inside of the head looks like this now 



Then assemble the neck with the head like this



## Body

First screw on `body_middle_bottom`

Capture d’écran du 2025-02-09 12-10-00

Then insert the M3 inserts in all the holes of `body_middle_bottom` and `body_middle_top` on which we'll mount the battery pack and `body_front`.

Then mount `body_middle_top`, `body_front` and the battery pack

<table>
  <tr>
    <td> </td>
    <td> </td>
   </tr> 
</table>

Et voila :) 

<table>
  <tr>
    <td> </td>
    <td> </td>
   </tr> 
</table>

> Now that your duck is fully assembled, you setup the raspberry pi and the runtime software [here](https://github.com/apirrone/Open_Duck_Mini_Runtime)

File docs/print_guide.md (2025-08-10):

# Print guide

You can find the `.stl` files under the `print/` directory at the root of this repo. 

All the parts are printed in standard PLA with 15% infill, except for `foot_bottom_tpu.stl`, which is to be printed in TPU at 40% infill.

## Parts to print
- foot_top.stl x2
- foot_side.stl x2
- foot_bottom_pla.stl x2
- foot_bottom_tpu.stl x2 (TPU)
- knee_to_ankle_left_sheet.stl x4
- knee_to_ankle_right_sheet.stl x4
- leg_spacer.stl x4
- left_roll_to_pitch.stl x1
- right_roll_to_pitch.stl x1
- roll_motor_bottom.stl x2
- roll_motor_top.stl x2
- trunk_bottom.stl x1
- trunk_top.stl x1
- neck_left_sheet.stl x1
- neck_right_sheet.stl x1
- head_pitch_to_yaw.stl x1
- head_yaw_to_roll.stl x1
- head_roll_mount.stl x1
- head.stl x1
- head_bot_sheet.stl x1
- left_antenna_holder.stl x1
- right_antenna_holder.stl x1
- left_cache.stl x1
- right_cache.stl x1
- body_front.stl x1
- body_middle_bottom.stl x1
- body_middle_top.stl x1
- body_back.stl x1
- battery_pack_lid.stl x1
- bulb.stl x1
- flash_light_module.stl x1
- flash_reflector_interface.stl x1
- left_eye.stl x1
- right_eye.stl x1
- speaker_interface.stl x1
- speaker_stand.stl x1

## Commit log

2025-09-08 add wild robot export
    [21700.stl, battery_hook.stl, battery_servo_connect.stl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]
2025-09-14 add wild mujoco
    [cell.stl, low_leg_left.stl, low_leg_right.stl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]
2025-09-14 update wild
    [antenna.stl, battery_pack_lid.stl, bms.stl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]
2025-09-15 update wild mujoco
    [frame.stl, htd_45h_1circle.stl, icm45686.stl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]
